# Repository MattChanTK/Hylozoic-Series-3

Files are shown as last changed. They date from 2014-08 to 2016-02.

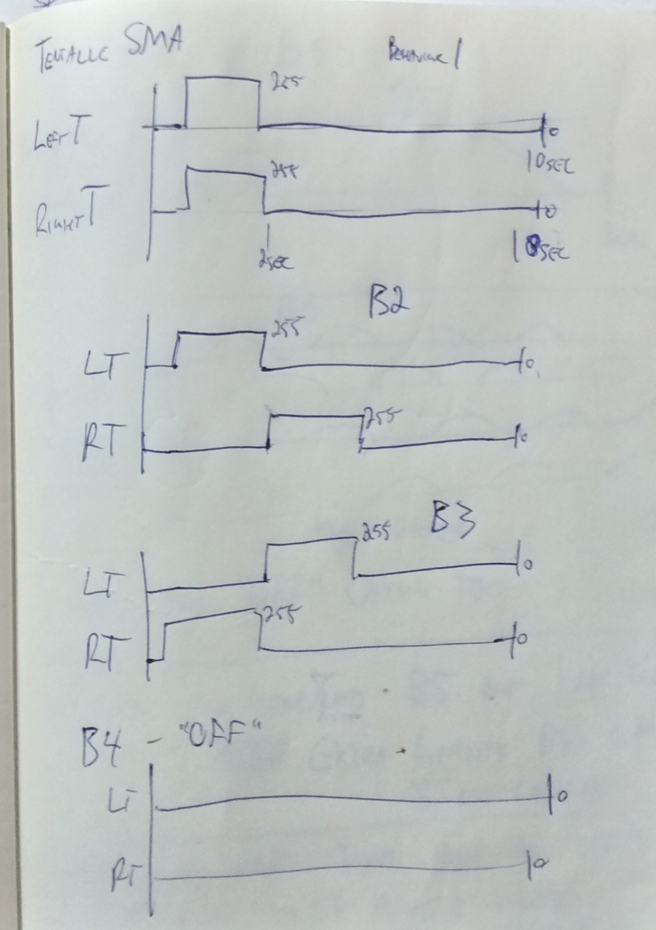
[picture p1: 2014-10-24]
Software/teensy_firmware/HK_Unit_Teensy/Wave_form_sketch.jpg

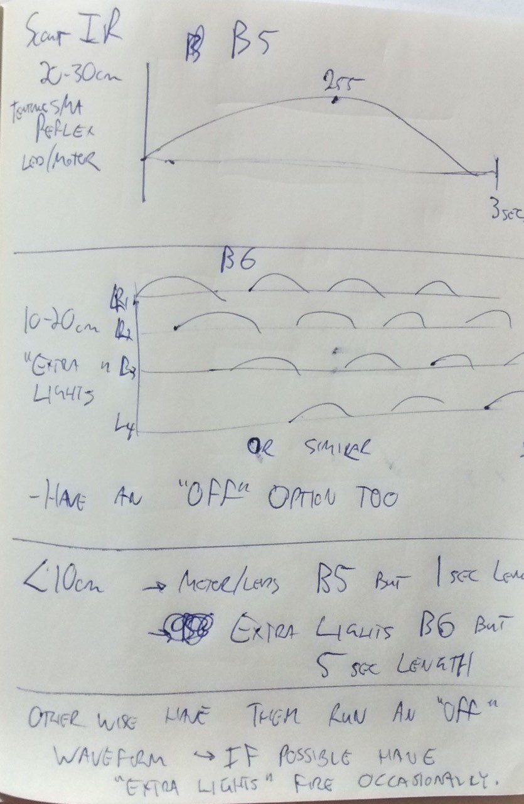
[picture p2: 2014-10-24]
Software/teensy_firmware/HK_Unit_Teensy/Wave_form_sketch_2.jpg

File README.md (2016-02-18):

Hylozoic Series 3 Interactive Control System
======================

 Combining techniques in architecture, the arts, electronics, and software, the Living Architecture System Group (LASG) develops interactive art sculptures that engage occupants in an immersive environment. The overarching goal of this research is to develop architectural systems that possess life-like qualities. In the Hylozoic Series kinetic sculptures built by [Philip Beesley Architect Inc.](http://philipbeesleyarchitect.com/), the designers use a network of microcontrollers to control and sample a sizable number of actuators and sensors. Each node in the network can perform a simple set of interactive behaviours. Though complexity may emerge in previous systems through superposition of a set of simple and prescripted behaviours, the responses of the systems to occupants remain rather robotic and ultimately dictated by the will of the designers. 

To enable the sculpture to automatically generate interactive behaviours and
adapt to changes, [Curiosity-Based Learning Algorithm (CBLA)](https://ece.uwaterloo.ca/~dkulic/pubs/ChanIROS2015.pdf), a reinforcement learning algorithm which selects actions that lead to maximum potential knowledge gains, is introduced.

To realize the CBLA system on a physical interactive art sculpture, an overhaul of the previous series’ interactive control hardware was necessary. CBLA requires the system to be able to sense the consequences of its own actions and its surrounding at a much higher resolution and frequency than previously implemented behaviour algorithms. This translates to the need to interface and collect samples from a substantially larger number of sensors. 

The **Hylozoic Series 3 Interactive Control System** consists of a new set of hardware and control system software was developed. It enables the control and sampling of hundreds of devices on a centralized computer through USB connections. Moving the computation from an embedded platform simpliﬁes the implementation of the CBLA system, which is a computationally intensive and complex
program. In addition, the large amount of data generated by the system can now be recorded without sacriﬁcing response time nor resolution.

## Organizations

### Hardware

The electronics that interface with the sensors and actuators were mostly customly designed. The [schematic](Hardware/Design Files), [PCB design](Hardware/Design Files), BOM, as well as [fabrication files](Hardware/fabrication) (like Gerber and quotes) for previous production runs can be found in the [Hardware](Hardware) directory. 

### Software

The [firmware](Software/teensy_firmware) that runs on the Teensy microcontroller, the [Python-based software framework](Software/pyHylozoic3) (pyHylozoic3), and [installation-specific behaviours](Software/complex_behaviours) can be found in the [Software](Software) directory. In addition, some of the necessary [libraries](Software/_libraries), and some [basic demo codes](Software/basic_behaviours) can also be in the directory.

In addition to the [communication framework](Software/pyHylozoic3/interactive_system/interactive_system), the pyHylozoic3 module includes an implemenation of the [CBLA Engine](Software/pyHylozoic3/cbla/cbla/cbla_engine), and [Abstract Node system](Software/pyHylozoic3/abstract_node/abstract_node) that supports the deployments of a network of multiple [CBLA Nodes](Software/pyHylozoic3/cbla/cbla).

## Contributors
* Matthew Tsz Kiu Chan (University of Waterloo)
* Mohammedreza Memarian (University of Waterloo)
* Matt Borland (Philip Beesley Architect Inc.)
* David Kadish (Philip Beesley Architect Inc.)

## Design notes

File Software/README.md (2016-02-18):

# Hylozoic Series 3 Software

## pyHylozoic3

The pyHylozoic3 directory is a set of Python Modules that make up the Hylozoic Series 3 software framework and its key features. It is written for Python 3.4+ (with libraries packaged with [Anaconda](https://www.continuum.io/downloads)) and tested on Windows 7, 8, 8.1, and 10. To install, run the [*install_pyHylozoic3.bat*](pyHylozoic3/install_pyHylozoic3.bat). To communicate with Teensy devices over USB, [libusb0.1](http://www.libusb.org/) is also required. Its installation files for Windows PC can be found in the [libraries](_libraries) directory.

## Firmware (teensy_firmware)

For different hardware configurations, different firmware (written in Arduino/C++) is required. This firmware goes with a matching set of [pyHylozoic3](pyHylozoic3) based communication protocol and behaviours code. Common utilities and base class files can be found in the [libraries](libraries) directory.

In the [teensy_firmware](teensy_firmware) directory, there are also standalone software that does not require the use of [pyHylozoic3](pyHylozoic3).

## Complex Behaviours (complex_behaviours)

Complex projects that use the [abstract_node](pyHylozoic3/abstract_node/abstract_node) module in the [pyHylozoic3](pyHylozoic3) are located in the [complex_behaviours](complex_behaviours) directory. This includes system that runs [CBLA](pyHylozoic3/cbla/cbla) and more elaborate prescripted behaviours. In addition, [hmi_gui](pyHylozoic3/hmi_gui/hmi_gui) can also be used to create a simple GUI that outputs internal data and basic textbox-based controls.

## Basic Behaviours (basic_behaviours)

Simple test or demo codes that only uses the [interactive_system](pyHylozoic3/interactive_system) module are found in the [basic_behaviours](basic_behaviours) directory.
Example basic behaviours include [basic actuation cycling](basic_behaviours/Behaviours.py), [End-Of-Line testing script](basic_behaviours/EOL_Tool.py), and [internode test](basic_behaviours/Behaviours.py) that demonstrated the possibilibity of nehgbourhood behaviours.

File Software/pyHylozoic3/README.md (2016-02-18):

# pyHylozoic3

## Interactive System ([interactive_system](interactive_system/interactive_system))

It is a Python module that was written to enable the communication with many Teensy devices simultaneously. A Teensy-Interface thread is created for each Teensy device and synchronize the copies of the hash tables on the Teensy and the computer continuously. Applications on the computer side can control and sample the states of the Teensy devices by modifying the values in the hash tables.

## Abstract Node Layer ([abstract_node](abstract_node/abstract_node))

An additional layer of abstraction was built to represent the sculpture as a network of node. Each node runs as its own thread and possesses a set of input and output variables. Behaviour of each node can be programmed individually. A pre-scripted version of the behaviours will be programmed to compare with the CBLA version in user studies.

## Curiosity Driven Learning Algorithm ([cbla](cbla/cbla))
The CBLA is a type of reinforcement learning algorithm, where the reduction of prediction error is the reward. During the learning process, it will explore regions of the state space that are neither too predictable nor too random; it wants to focus on areas that have the highest potential for new knowledge. To structure the learning process and identify interesting
regions of the state-space, the CBLA automatically segments the state-space into regions; an expert in each region makes predictions about the effects of an action and adjusts its prediction model based on the actual resultant state. The value of each expert is determined by its record of error reduction. This value will then determine the execution likelihood of the action associated with this expert.

## GUI ([hmi_gui](hmi_gui/hmi_gui), [custom_gui](custom_gui/custom_gui))
A basic GUI that display values of input, output, and internal variables. It's based on [Tkinter](https://wiki.python.org/moin/TkInter). A textbox can also be added to change values of the the output variables. *custom_gui* implemented installation-specific GUI.

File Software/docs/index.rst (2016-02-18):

.. Hylozoic Series 3 documentation master file, created by
   sphinx-quickstart on Thu Jan 28 16:36:26 2016.
   You can adapt this file completely to your liking, but it should at least
   contain the root `toctree` directive.

Welcome to Hylozoic Series 3's documentation!
=============================================

**pyHylozoic3** is a set of Python modules that provide the key features introduced in the Hylozoic Series 3 system. 

- interactive_system_ provides the infrastructures that enable a client running a pyHylozoic3 program to communicate with a distributed set of microconstrollers.

- abstract_node_ enables the creation of a network of asychronous threads that describe the behaviour of the system.

- hmi_gui_ provides a basic GUI that is compatible the *abstract_node* system.

- custom_gui_ provides a set of customized GUI based on *hmi_gui* that tailors to a handful of operation modes.

- cbla_ contains the CBLA Engine and the implementation of a generic CBLA Node.

.. _interactive_system: ./_apidoc/interactive_system/modules.html
.. _abstract_node: ./_apidoc/abstract_node/modules.html
.. _hmi_gui: ./_apidoc/hmi_gui/modules.html
.. _custom_gui: ./_apidoc/custom_gui/modules.html
.. _cbla: ./_apidoc/cbla/modules.html

**complex_behaviours** contains a handful of specific implementations that use the *pyHylozoic3* Module.

- *pbai_fin_test_bed* contains the implementation of manual, prescipted, and CBLA type behaviours for the CBLA Fin Test Bed.

- *cbla_test_bed* contains the implementation of CBLA behaviours for the CBLA Test Bed used during development and validation of the CBLA. This behaviour does not use the *cbla* module in *pyHylozoic3*. Instead, its CBLA Engine and CBLA Nodes are embedded to protect the integrity of the system.

- *washington_demo* contains the work-in-progress for the Sound Test Bed that is primarily used for demostration purposes in Washington and perhaps CITA.

Contents:

.. toctree::
   :maxdepth: 2
   
   ./installing

Communications Protocol
=======================
There is no standard protocol because every configuration has a different set of hardware attached.
So for each installation, we would need to write a different set of protocols.
   
Terminology
===========
Nodes are hierarchial and can comprise of other nodes (i.e. nodes can be sets of nodes).
But at their most basic level each sensor or actuator can be its own node and nodes can consist of inputs and/or outputs.

Indices and tables
==================

* :ref:`genindex`
* :ref:`modindex`
* :ref:`search`

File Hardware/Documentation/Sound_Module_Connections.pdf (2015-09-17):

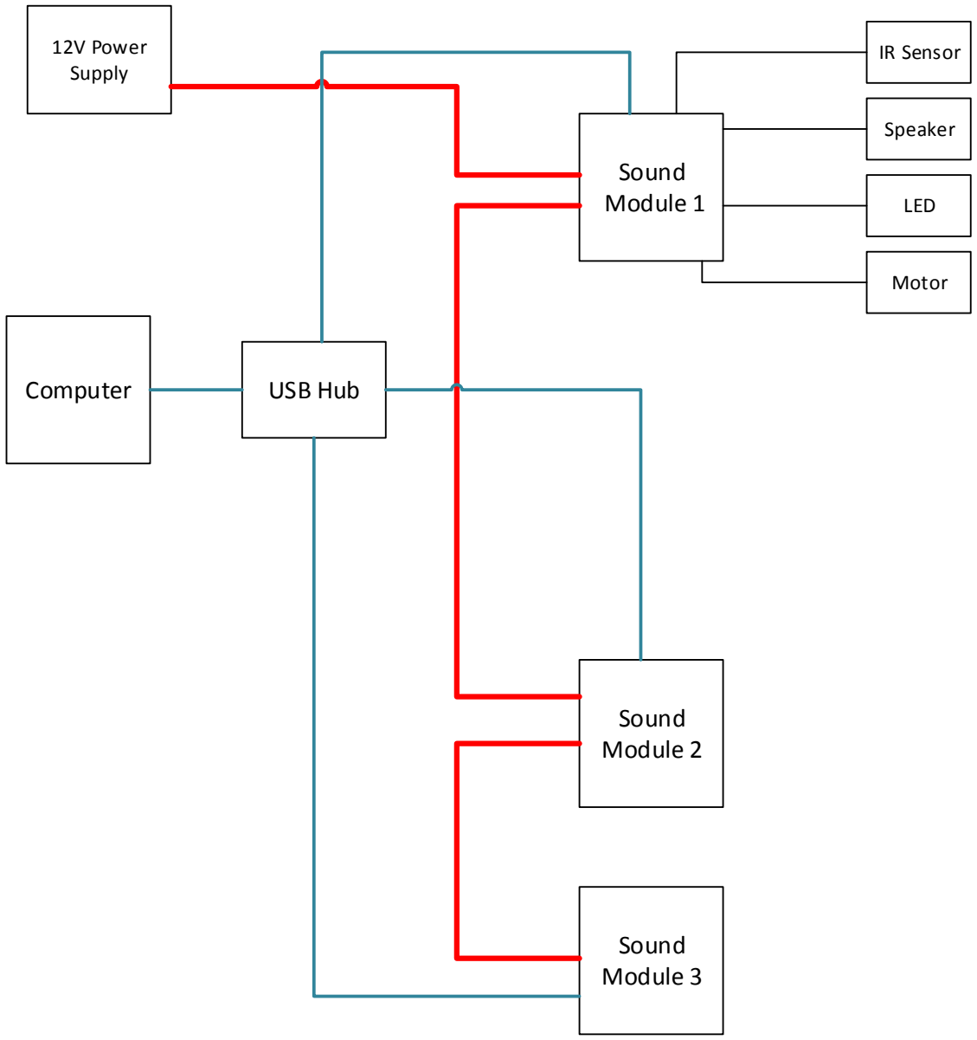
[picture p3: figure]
Sound Module 1; 12V Power Supply; Sound Module 2; Sound Module 3; Computer; USB Hub; IR Sensor; Speaker; LED; Motor

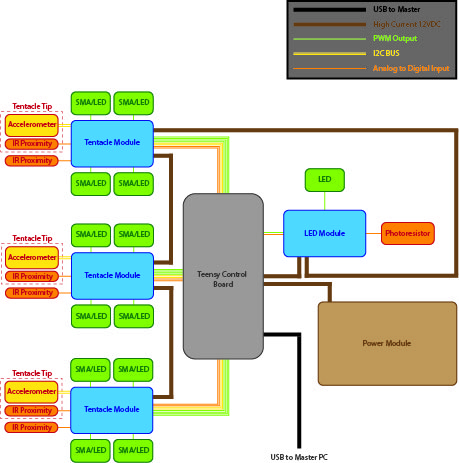
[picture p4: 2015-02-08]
Hardware/Documentation/High-level Electronic Block Diagram.jpg

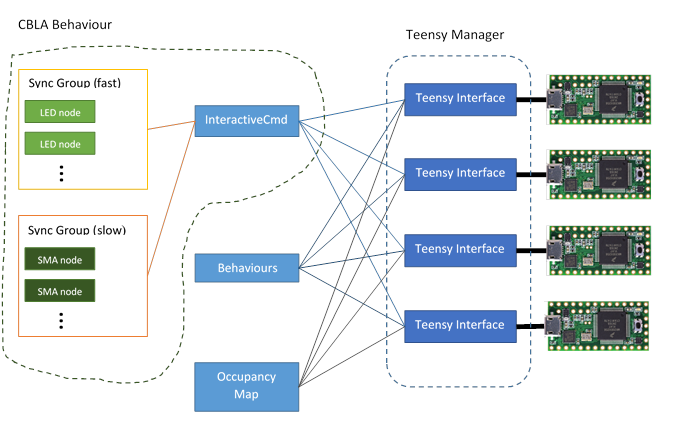
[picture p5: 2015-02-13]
Software/_documentation/diagrams/Software Overall Network Architecture.png

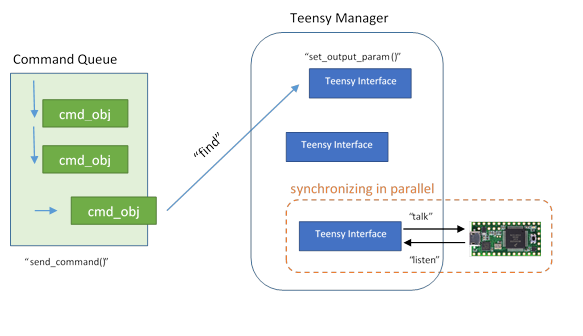
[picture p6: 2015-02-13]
Software/_documentation/diagrams/Software InteractiveCmd Block Diagram.png

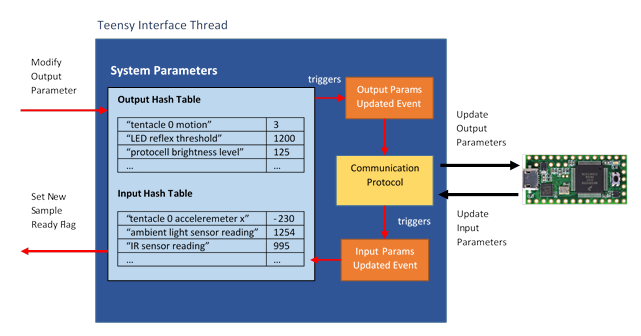
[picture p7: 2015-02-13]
Software/_documentation/diagrams/Software Teensy Interface Block Diagram.png

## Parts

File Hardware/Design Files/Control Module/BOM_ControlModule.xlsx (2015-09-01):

 | Control Module Bill of Materials (BOM)
Item # | Ref Des | Description | Qty | Manufacturer | Mfg Part # | Package | Type | Your Instructions | Total Required for 10 Boards | Packed
1 | JP2, JP3 | CONN HEADER .100" SNGL STR 3POS | 2 | Sullins Connector Solutions | PREC003SAAN-RC | 0.100" (2.54mm) | thru-hole |  | 20 | 24
2 | LED1, LED2, LED3 | LED 3.2X1.6MM 568NM GRN CLR SMD | 3 | Kingbright | APTR3216SGC | 1206 | SMD |  | 30 | 34
3 | SV3, SV4, SV5, SV6, SV7, SV8 | CONN HEADER FEMALE 8 POS .1" TIN | 6 | Sullins Connector Solutions | PPTC081LFBN-RC | 0.100" (2.54mm) | thru-hole |  | 0 | 0
4 | X1 | CONN HEADER FEMALE 2 POS .1" TIN | 1 | Sullins Connector Solutions | PPTC021LFBN-RC | 0.100" (2.54mm) | thru-hole |  | 0 | 0
5 | X7, X9 | TERMINAL BLOCK 5.08MM 2POS PCB | 4 | On Shore Technology Inc | OSTTG025100B | 0.200" pitch | thru-hole |  | 40 | 0
6 | C4, C5 | CAP CER 0.1UF 50V Y5V 0603 | 2 | Samsung Electro-Mechanics America, Inc | CL10F104ZB8NNNC | 0603 | SMD |  | 20 | 20
7 | C2, C3 | CAP CER 1UF 25V 10% X5R 0603 | 2 | Murata Electronics North America | GRM188R61E105KA12D | 0603 | SMD |  | 20 | 20
8 | R7, R8 | RES 2.2K OHM 1/10W 5% 0603 | 2 | Samsung Electro-Mechanics America, Inc | RC1608J222CS | 0603 | SMD |  | 20 | 20
9 | R1, R4, R5 | RES 470 OHM 1/4W 5% 0603 SMD | 3 | Rohm Semiconductor | RHM470DCT-ND | 0603 | SMD |  | 30 | 30
10 | C1 | CAP ALUM 470UF 25V 20% RADIAL | 1 | Panasonic Electronic Components | EEU-FR1E471Y | 0.315" Dia | thru-hole |  | 10 | 13
11 | R2, R3, R6 | RES 4.7K OHM 1/10W 5% 0603 SMD | 3 | Yageo | RC0603JR-074K7L | 0603 | SMD |  | 30 | 30
12 | U2, U3 | IC MUX/DEMUX 8X1 16TSSOP | 2 | NXP Semiconductors | 74HC4051PW,118 | 16-TSSOP | SMD |  | 20 | 20
13 | IC1 | IC REG LDO 5V 1A DPAK | 1 | ON Semiconductor | MC7805BDTRKG | TO-252-3 | SMD |  | 10 | 10
14 | U1 | IC PWM CTLR LED DVR 28TSSOP | 1 | NXP Semiconductors | PCA9685PW/Q900,118 | 28-TSSOP | SMD |  | 10 | 10
15 | Q1 | MOSFET N-CH 60V 300MA SOT-23 | 1 | Vishay Siliconix | 2N7002K-T1-E3TR-ND | SOT-23-3 |  |  | 10 | 14
16 | SV1 | CONN HEADER FEMALE 4POS .1" TIN | 1 | Sullins Connector Solutions | PPTC041LFBN-RC | 0.100" (2.54mm) | thru-hole |  | 10 | 0
17 | D1 | DIODE SCHOTTKY 40V 5A DO201AD | 1 | Comchip Technology | SB540E-G | DO-201AD, Axial | thru-hole |  | 10 | 12
18 | SV2 | CONN HEADER FMALE 8PS .1" DL TIN | 1 | Sullins Connector Solutions | PPTC042LFBN-RC | 0.100" (2.54mm) | thru-hole |  | 10 | 0
19 | U$2 | CONN HEADER FEMALE 3 POS .1" TIN | 1 | Sullins Connector Solutions | PPPC031LFBN-RC | 0.100" (2.54mm) | thru-hole |  | 10 | 10
 |  | CONN HEADER FEMALE 5 POS .1" TIN | 3 | Sullins Connector Solutions | PPTC051LFBN-RC | 0.100" (2.54mm) | thru-hole |  | 30 | 0
 |  | CONN HEADER FEMALE 13 POS .1" TIN | 2 | Sullins Connector Solutions | PPTC131LFBN-RC | 0.100" (2.54mm) | thru-hole |  | 20 | 0
20 | IC2 | IC REG LDO 3.3V 0.5A TO252-3 | 1 | Texas Instruments | UA78M33CKVURG3 | TO-252-3 | SMD |  | 10 | 12
21 | X8 | CONN HEADER FEMALE 2 POS .1" TIN | 1 | Sullins Connector Solutions | PPTC021LFBN-RC | 0.100" (2.54mm) | thru-hole |  | 0 | 0

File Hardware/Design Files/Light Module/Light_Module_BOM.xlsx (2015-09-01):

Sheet: Light Module
 | Light Module Bill of Materials (BOM)
Item # | Ref Des | Description | Qty | Manufacturer | Mfg Part # | Package | Type | Your Instructions
1 | X8 | CONN MOD JACK 4P4C VERT UNSHLD | 1 | Assmann WSW Components | A-2014-3-4-N-T-R |  | thru-hole
2 | JP1 | CONN HEADER .100" SNGL STR 3POS | 1 | Sullins Connector Solutions | PREC003SAAN-RC | 0.100" (2.54mm) | thru-hole
3 | LED1 | LED 3.2X1.6MM 568NM GRN CLR SMD | 1 | Kingbright | APTR3216SGC | 1206 | SMD
4 | T1 | MOSFET N-CH 60V 18A 43MOHM DPAK | 1 | ON Semiconductor | NTD5867NLT4G | TO-252-3 | SMD
5 | X4 | CONN HEADER MALE 2 POS .1" TIN | 1 | Sullins Connector Solutions | PREC002SAAN-RC | 0.100" (2.54mm) | thru-hole
6 | X7 | CONN HEADER MALE 3 POS .1" TIN | 1 | Sullins Connector Solutions | PREC003SAAN-RC | 0.100" (2.54mm) | thru-hole
7 | X1 | TERMINAL BLOCK 5.08MM 2POS PCB | 2 | On Shore Technology Inc | OSTTG025100B | 0.200" pitch | thru-hole
8 | X6 | TERMINAL BLOCK 5.08MM 2POS PCB | 1 | On Shore Technology Inc | OSTTG025100B | 0.200" pitch | thru-hole
9 | C2, C3 | CAP CER 1UF 25V 10% X5R 0603 | 2 | Murata Electronics North America | GRM188R61E105KA12D | 0603 | SMD
10 | R2 | RES 4.7K OHM 1/10W 5% 0603 SMD | 1 | Yageo | RC0603JR-074K7L | 0603 | SMD
11 | R1 | RES 470 OHM 1/4W 5% 0603 SMD | 1 | Rohm Semiconductor | RHM470DCT-ND | 0603 | SMD
12 | C1 | CAP ALUM 470UF 25V 20% RADIAL | 1 | Panasonic Electronic Components | EEU-FR1E471Y | 0.315" Dia | thru-hole
13 | R3 | RES 5.6 OHM 5W 5% AXIAL | 1 | Yageo | SQP500JB-5R6 |  | thru-hole
14 | IC1 | IC REG LDO 5V 1A DPAK | 1 | ON Semiconductor | MC7805BDTG | TO-252-3 | SMD
15 | X3 | CONN MOD JACK R/A 8P8C | 1 | FCI | 54602-908LF |  | thru-hole
16 | D1 | DIODE SCHOTTKY 40V 5A DO201AD | 1 | Comchip Technology | SB540E-G | DO-201AD, Axial | thru-hole

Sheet: Sheet1
 | Light Module Bill of Materials (BOM)
Item | Ref Des | Description | Value | Qty | Device | Package
1 | X8 | AMP connector |  | 1 | 558872-1
1 | JP1 | JUMPER |  | 1 | JP2E
1 | LED1 | LED |  | 1 | LEDSML1206
1 | T1 | MOS FET |  | 1 | NTD5867NLT4G
1 | X4 | PIN HEADER |  | 1 | PINHD-1X2
1 | X7 | PIN HEADER |  | 1 | PINHD-1X3
1 | X1 | WAGO SREW CLAMP |  | 1 | W237-04P
1 | X6 | WAGO SCREW CLAMP |  | 1 | W237-102
2 | C2, C3 | CAPACITOR, American symbol | 1uF | 2 | C-USC0603
1 | R2 | RESISTOR, American symbol | 4.7k | 1 | R-US_R0603
1 | R1 | RESISTOR, American symbol | 470 | 1 | R-US_R0603
1 | C1 | POLARIZED CAPACITOR, American symbol | 470uF | 1 | CPOL-USE5-10.5
1 | R3 |  | 5.6 | 1 | SQP500JB-5R6
1 | IC1 | 1A Positive Voltage Regulators | MC7805BDTRKG | 1 | MC7805BDTRKG
1 | X3 | CORCOM Modular RJ Jacks No Shield | RJ45-8X | 1 | RJ45-8X
1 | D1 | SCHOTTKY BARRIER RECTIFIER 3.0 AMPERES 20, 30, 40 VOLT | SB540E-G | 1 | SB540E-G

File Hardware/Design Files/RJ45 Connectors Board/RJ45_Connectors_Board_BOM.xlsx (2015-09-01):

 | RJ45 Connector Board Bill of Materials (BOM)
Item # | Ref Des | Description | Qty | Manufacturer | Mfg Part # | Package | Type | Your Instructions | Total Required for 10 Boards | Packed
1 | LED1, LED2, LED3, LED4, LED5, LED6, LED7, LED8, LED9, LED10, LED11, LED12, LED13, LED14, LED15, LED16, LED17, LED18, LED19, LED20, LED21, LED22, LED23, LED24 | LED 3.2X1.6MM 568NM GRN CLR SMD | 24 | Kingbright | APTR3216SGC | 1206 | SMD |  | 240 | 0
2 | SV1, SV2, SV9, SV10, SV11, SV12 | CONN HEADER .100" SNGL STR 8POS | 6 | Sullins Connector Solutions | PREC008SAAN-RC | 0.100" (2.54mm) | thru-hole |  | 60 | 0
3 | X1 | CONN HEADER .100" SNGL STR 2POS | 1 | Sullins Connector Solutions | PREC002SAAN-RC | 0.100" (2.54mm) | thru-hole |  | 10 | 0
4 | X2 | CONN HEADER .100" SNGL STR 3POS | 1 | Sullins Connector Solutions | PREC003SAAN-RC | 0.100" (2.54mm) | thru-hole |  | 10 | 0
5 | IC1, IC2, IC3 | TRANS 8NPN DARL 50V 0.5A 18SOL | 3 | Toshiba Semiconductor and Storage | ULN2803AFWG,C,EL | 18-SOIC | SMD |  | 30 | 0
6 | R1, R2, R3, R4, R5, R6, R7, R8, R9, R10, R11, R12, R13, R14, R15, R16, R17, R18, R19, R20, R21, R22, R23, R24 | RES 470 OHM 1/4W 5% 0603 SMD | 24 | Rohm Semiconductor | RHM470DCT-ND | 0603 | SMD |  | 240 | 0
7 | SV3, SV4, SV5, SV6, SV7, SV8 | CONN MOD JACK 8P8C VERT UNSHLD | 6 | FCI | 69255-001LF |  | thru-hole |  | 60 | 63

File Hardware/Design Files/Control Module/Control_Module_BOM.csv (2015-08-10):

Partlist
Exported from Control_Module.brd at 2015-08-10 3:16 PM
EAGLE Version 7.3.0 Copyright (c) 1988-2015 CadSoft
Assembly variant:
Part     Value                        Package            Library                    Position (inch)       Orientation
C1       470uF                        E5-10,5            rcl                        (0.99 0.24)           MR90
C2       1uF                          C0603              rcl                        (0.3 0.64)            R90
C3       1uF                          C0603              rcl                        (0.3 0.14)            R270
C4       100nF                        C0603              rcl                        (0.3 0.49)            R270
C5       100nF                        C0603              rcl                        (0.3 0.29)            R90
D1       SB540E-G                     DO201T15           CBLA_Test_bed_Library      (2.48 0.61)           R0
IC1      MC7805BDTRKG                 DPACK_3            CBLA_Test_bed_Library      (0.63 0.54)           R90
IC2      UA78M33CKVU                  DPACK              CBLA_Test_bed_Library      (0.63 0.19)           R90
JP2                                   JP2                jumper                     (0.98 0.64)           R90
JP3                                   JP2                jumper                     (1.93 0.59)           R0
LED1                                  SML1206            led                        (2.77 0.43)           MR180
LED2                                  SML1206            led                        (0.46 0.54)           MR0
LED3                                  SML1206            led                        (0.46 0.25)           MR0
Q1       PROGRAM_FET                  SOT-23             transistors                (0.96 2.04)           R180
R1       470                          R0603              CBLA_Test_bed_Library      (2.59 0.43)           MR180
R2       4k7                          R0603              CBLA_Test_bed_Library      (1.16 0.61)           R270
R3       4k7                          R0603              CBLA_Test_bed_Library      (1.71 0.72)           R0
R4       470                          R0603              CBLA_Test_bed_Library      (0.47 0.13)           MR180
R5       470                          R0603              CBLA_Test_bed_Library      (0.46 0.44)           MR180
R6       4k7                          R0603              CBLA_Test_bed_Library      (0.97 2.21)           R0
R7       2.2k                         R0603              CBLA_Test_bed_Library      (1.08 1.32)           R270
R8       2.2k                         R0603              CBLA_Test_bed_Library      (1.85 1.69)           R270
SV1      PWM_I2C                      MA04-1             con-lstb                   (1.43 0.64)           R0
SV2      SPI                          MA04-2             con-lstb                   (0.71 2.99)           R0
SV3                                   MA08-1             con-lstb                   (0.18 2.69)           R270
SV4                                   MA08-1             con-lstb                   (0.18 1.89)           R270
SV5                                   MA08-1             con-lstb                   (0.18 1.09)           R270
SV6                                   MA08-1             con-lstb                   (2.78 2.69)           R90
SV7                                   MA08-1             con-lstb                   (2.78 1.89)           R90
SV8                                   MA08-1             con-lstb                   (2.78 1.09)           R90
U$2      TEENSY_3.1_ALL_PINS_AND_PADS TEENSY_3.1_ALLPINS Teensy_3_Series_Board_v1.0 (1.43 2.34)           R0
U1       PCA9685PW                    SOP65P640X110-28N  NXP_By_element14_Batch_1   (1.43 0.94)           R0
U2       74HC4051PW,118               SOP65P640X110-16N  NXP_By_element14_Batch_1   (1.43 1.29)           R0
U3       74HC4051PW,118               SOP65P640X110-16N  NXP_By_element14_Batch_1   (1.43 1.54)           R0
X1                                    1X02               CBLA_Test_bed_Library      (1.85 3.04)           R90
X7                                    W237-4P            con-wago-508               (2.47 0.2)            R0
X8       UART                         1X02               CBLA_Test_bed_Library      (1 2.99)              R90
X9                                    W237-4P            con-wago-508               (1.61 0.2)            R0

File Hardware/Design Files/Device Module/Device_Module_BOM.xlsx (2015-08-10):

 | Device Module Bill of Materials (BOM)
Item # | Ref Des | Description | Qty | Manufacturer | Mfg Part # | Package | Type | Your Instructions | Total Required for 22 Boards | Packed
1 | JP1, JP2, JP3 | CONN HEADER .100" SNGL STR 3POS | 3 | Sullins Connector Solutions | PREC003SAAN-RC | 0.100" (2.54mm) | thru-hole |  | 66 | 0
2 | LED1, LED2, LED3, LED4, LED5, LED6 | LED 3.2X1.6MM 568NM GRN CLR SMD | 6 | Kingbright | APTR3216SGC | 1206 | SMD |  | 132 | 140
3 | X11, X12, X13, X14 | PIN HEADER | 1 |  |  | 0.100" (2.54mm) | thru-hole | Leave unpopulated | 0 | 0
4 | X2 | CONN HEADER .100" SNGL STR 3POS | 1 |  |  | 0.100" (2.54mm) | thru-hole | Leave unpopulated | 0 | 0
5 | X15 | CONN HEADER .100" SNGL STR 3POS | 1 | PREC003SAAN-RC | PREC020SAAN-RC | 0.100" (2.54mm) | thru-hole |  | 22 | 0
6 | X4, X6 | CONN HEADER FEMALE 8POS .1" TIN | 2 | Sullins Connector Solutions | PPTC081LFBN-RC | 0.100" (2.54mm) | thru-hole |  | 44 | 0
7 | X1 | TERMINAL BLOCK 5.08MM 2POS PCB | 2 | On Shore Technology Inc | OSTTG025100B | 0.200" pitch | thru-hole | Put two 2p together to form a 4p | 44 | 120
8 | X7, X8, X9, X10 | TERMINAL BLOCK 5.08MM 2POS PCB | 4 | On Shore Technology Inc | OSTTG025100B | 0.200" pitch | thru-hole |  | 88
9 | C4, C5 | CAP CER 0.1UF 50V Y5V 0603 | 2 | Samsung Electro-Mechanics America, Inc | CL10F104ZB8NNNC | 0603 | SMD |  | 44 | 50
10 | C2, C3, C6, C7, C8, C9 | CAP CER 10UF 25V 10% X5R 1206 | 6 | Samsung Electro-Mechanics America, Inc | CL31A106KAHNNNE | 1206 | SMD |  | 132 | 140
11 | R4, R5, R6, R7 | RES 1.00K OHM .25W 1% 0603 SMD | 4 | Vishay Dale | CRCW06031K00FKEAHP | 0603 | SMD |  | 88 | 92
12 | R1 | RES 267 OHM 1/10W .1% 0603 SMD | 1 | Panasonic Electronic Components | ERA-3AEB2670V | 0603 | SMD |  | 22 | 25
13 | R8, R9, R10, R11 | RES 4.7K OHM 1/10W 5% 0603 SMD | 4 | Yageo | RC0603JR-074K7L | 0603 | SMD |  | 88 | 93
14 | R2, R3, R12, R13, R14, R15 | RES 470 OHM 1/4W 5% 0603 SMD | 6 | Rohm Semiconductor | RHM470DCT-ND | 0603 | SMD |  | 132 | 136
15 | C1 | CAP ALUM 470UF 25V 20% RADIAL | 1 | Panasonic Electronic Components | EEU-FR1E471Y | 0.315" Dia | thru-hole |  | 22 | 24
16 | IC2 | IC REG LDO 5V 1A DPAK | 1 | ON Semiconductor | MC7805BDTG | TO-252-3 | SMD |  | 22 | 24
17 | T1, T2, T3, T4 | MOSFET N-CH 60V 18A 43MOHM DPAK | 4 | ON Semiconductor | NTD5867NLT4G | TO-252-3 | SMD |  | 88 | 100
18 | IC1 | CONV DC/DC 6A 12VIN POL SIP | 1 | Murata Power Solutions Inc | OKR-T/6-W12-C | 5-SIP Module | thru-hole |  | 22 | 24
19 | X3, X5 | CONN MOD JACK R/A 8P8C | 2 | FCI | 54602-908LF |  | thru-hole |  | 44 | 50
20 | D1 | DIODE SCHOTTKY 40V 5A DO201AD | 1 | Comchip Technology | SB540E-G | DO-201AD, Axial | thru-hole |  | 22 | 24
21 | IC3 | IC REG LDO 3.3V 0.5A TO252-3 | 1 | Texas Instruments | UA78M33CKVURG3 | TO-252-3 | SMD |  | 22 | 25

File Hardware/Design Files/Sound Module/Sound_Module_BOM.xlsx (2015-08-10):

 | Sound Module Bill of Materials (BOM)_Bittele Electronics Inc.
Item # | Ref Des | Description | Qty | Manufacturer | Mfg Part # | Package | Type | Your Instructions | Total Required for 14 Boards | Packed
1 | LED1, LED2, LED3, LED4, LED5, LED6, LED7 | LED 3.2X1.6MM 568NM GRN CLR SMD | 7 | Kingbright | APTR3216SGC | 1206 | SMD |  | 98 | 100
2 | PINOUT | CONN HEADER .100" SNGL STR 8POS | 1 | Sullins Connector Solutions | PREC008SAAN-RC | 0.100" (2.54mm) | thru-hole |  | 14 | 0
3 | IC1, IC2, IC3, IC4 | IC REG LDO 5V 1A DPAK | 4 | IC REG LDO 5V 1A DPAK | MC7805BDTRKG |  |  |  | 56 | 60
4 | MOS1, MOS2 | MOSFET N-CH 60V 18A 43MOHM DPAK | 2 | ON Semiconductor | NTD5867NLT4G | TO-252-3 | SMD |  | 28 | 31
5 | AMP_1_2, AMP_2_2 | CONN HEADER .100" SNGL STR 2POS | 2 | Sullins Connector Solutions | PREC002SAAN-RC | 0.100" (2.54mm) | thru-hole |  | 28 | 0
6 | A_1, A_2, A_3, POWER_LED, X2, X3 | CONN HEADER .100" SNGL STR 3POS | 6 | Sullins Connector Solutions | PREC003SAAN-RC | 0.100" (2.54mm) | thru-hole |  | 84 | 0
7 | SD_1, SD_2 | CONN HEADER .100" SNGL STR 5POS | 2 | Sullins Connector Solutions | PREC005SAAN-RC | 0.100" (2.54mm) | thru-hole |  | 28 | 0
8 | AMP_1_1, AMP_2_1 | CONN HEADER .100" SNGL STR 7POS | 2 | Sullins Connector Solutions | PREC007SAAN-RC | 0.100" (2.54mm) | thru-hole |  | 28 | 0
9 | TAB_CONN | CONN HEADER .100" SNGL STR 5POS | 2 | Sullins Connector Solutions | PREC005SAAN-RC | 0.100" (2.54mm) | thru-hole | Put two single-row to make one double-row | 28 | 0
10 | POWER | TERMINAL BLOCK 5.08MM 2POS PCB | 2 | On Shore Technology Inc | OSTTG025100B | 0.200" pitch | thru-hole | Put two 2p together to form a 4p | 28 | 30
11 | R4, R6, R15 | RES SMD 10 OHM 1% 1/10W 0603 | 3 | Bourns Inc. | CR0603-FX-10R0GLFCT-ND | 0603 | SMD |  | 42 | 45
12 | C4, C5, C7, C12 | CAP CER 0.1UF 50V Y5V 0603 | 4 | Samsung Electro-Mechanics America, Inc | CL10F104ZB8NNNC | 0603 | SMD |  | 56 | 60
13 | R11, R13 | RES 1.00K OHM .25W 1% 0603 SMD | 2 | Vishay Dale | CRCW06031K00FKEAHP | 0603 | SMD |  | 28 | 32
14 | PWM1, PWM2, SPK-1, SPK-2 | TERMINAL BLOCK 3.5MM 2POS PCB | 4 | OSTTG025100B | OSTTG025100B | 3.5 mm pitch | thru-hole |  | 56 | 0
15 | C2, C3, C6, C11 | CAP CER 1UF 25V 10% X5R 0603 | 4 | Murata Electronics North America | GRM188R61E105KA12D | 0603 | SMD |  | 56 | 60
16 | R7, R8 | RES 2.2K OHM 1/10W 5% 0603 | 2 | Samsung Electro-Mechanics America, Inc | RC1608J222CS | 0603 | SMD |  | 28 | 32
17 | C1 | CAP ALUM 1000UF 25V 20% RADIAL | 1 | Panasonic Electronic Components | ECA-1EM102 | 0.394" Dia | thru-hole |  | 14 | 16
18 | R10, R12 | RES 4.7K OHM 1/10W 5% 0603 SMD | 2 | Yageo | RC0603JR-074K7L | 0603 | SMD |  | 28 | 32
19 | R1, R2, R3, R5, R14, R17, R18 | RES 470 OHM 1/4W 5% 0603 SMD | 7 | Rohm Semiconductor | RHM470DCT-ND | 0603 | SMD |  | 98 | 104
20 | C8, C9, C13 | CAP ALUM 470UF 25V 20% RADIAL | 3 | Panasonic Electronic Components | EEU-FR1E471Y | 0.315" Dia | thru-hole |  | 42 | 45
21 | TEENSY | CONN HEADER FEMALE 3 POS .1" TIN | 1 | Sullins Connector Solutions | PPPC031LFBN-RC | 0.100" (2.54mm) | thru-hole |  | 14 | 0
 |  | CONN HEADER FEMALE 5 POS .1" TIN | 3 | Sullins Connector Solutions | PPTC051LFBN-RC | 0.100" (2.54mm) | thru-hole |  | 42 | 0
 |  | CONN HEADER FEMALE 13 POS .1" TIN | 2 | Sullins Connector Solutions | PPTC131LFBN-RC | 0.100" (2.54mm) | thru-hole |  | 28 | 0
22 | JACK | CONN MOD JACK R/A 8P8C | 1 | FCI | 54602-908LF |  | thru-hole |  | 14 | 16
23 | D1 | DIODE SCHOTTKY 40V 5A DO201AD | 1 | Comchip Technology | SB540E-G | DO-201AD, Axial | thru-hole |  | 14 | 16

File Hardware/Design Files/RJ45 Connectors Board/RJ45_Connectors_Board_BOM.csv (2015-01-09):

Qty | Value | Device | Package | Parts | Description | MF | MPN | OC_FARNELL | OC_NEWARK
24 |  | LEDSML1206 | SML1206 | LED1, LED2, LED3, LED4, LED5, LED6, LED7, LED8, LED9, LED10, LED11, LED12, LED13, LED14, LED15, LED16, LED17, LED18, LED19, LED20, LED21, LED22, LED23, LED24 | LED
6 |  | MA08-1 | MA08-1 | SV1, SV2, SV9, SV10, SV11, SV12 | PIN HEADER |  |  | unknown | unknown
1 |  | PINHD-1X2 | 1X02 | X1 | PIN HEADER
1 |  | PINHD-1X3 | 1X03 | X2 | PIN HEADER
3 |  | ULN2803AFWG | SOP18 | IC1, IC2, IC3 | DRIVER ARRAY
24 | 470 | R-US_R0603 | R0603 | R1, R2, R3, R4, R5, R6, R7, R8, R9, R10, R11, R12, R13, R14, R15, R16, R17, R18, R19, R20, R21, R22, R23, R24 | RESISTOR, American symbol
6 | RJ45-8X | RJ45-8X | RJ45-NO-SHIELD | SV3, SV4, SV5, SV6, SV7, SV8 | CORCOM Modular RJ Jacks No Shield |  | RJ45-8X | unknown | 16R6101

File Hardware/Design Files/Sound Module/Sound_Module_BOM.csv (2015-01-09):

Qty | Value | Device | Package | Parts | Description | MF | MPN | OC_FARNELL | OC_NEWARK
7 |  | LEDSML1206 | SML1206 | LED1, LED2, LED3, LED4, LED5, LED6, LED7 | LED
1 |  | MA08-1 | MA08-1 | PINOUT | PIN HEADER |  |  | unknown | unknown
4 |  | MC7805BDTRKG | DPACK_3 | IC1, IC2, IC3, IC4 | 1A Positive Voltage Regulators
2 |  | NTD5867NLT4G | DPACK | MOS1, MOS2 | MOS FET
2 |  | PINHD-1X2 | 1X02 | AMP_1_2, AMP_2_2 | PIN HEADER
6 |  | PINHD-1X3 | 1X03 | A_1, A_2, A_3, POWER_LED, X2, X3 | PIN HEADER
2 |  | PINHD-1X5 | 1X05 | SD_1, SD_2 | PIN HEADER
2 |  | PINHD-1X7 | 1X07 | AMP_1_1, AMP_2_1 | PIN HEADER
1 |  | PINHD-2X5 | 2X05 | TAB_CONN | PIN HEADER
1 |  | W237-04P | W237-4P | POWER | WAGO SREW CLAMP |  |  | unknown | unknown
3 | 10 | R-US_R0603 | R0603 | R4, R6, R15 | RESISTOR, American symbol
4 | 100nF | C-USC0603 | C0603 | C4, C5, C7, C12 | CAPACITOR, American symbol
2 | 1K | R-US_R0603 | R0603 | R11, R13 | RESISTOR, American symbol
4 | 1X2-3.5MM | 1X2-3.5MM | 1X2-3.5MM | PWM1, PWM2, SPK-1, SPK-2 | 3.5mm Terminal block
4 | 1uF | C-USC0603 | C0603 | C2, C3, C6, C11 | CAPACITOR, American symbol
2 | 2.2k | R-US_R0603 | R0603 | R7, R8 | RESISTOR, American symbol
1 | 2000uF | CPOL-USE5-10.5 | E5-10,5 | C1 | POLARIZED CAPACITOR, American symbol
2 | 4.7K | R-US_R0603 | R0603 | R10, R12 | RESISTOR, American symbol
7 | 470 | R-US_R0603 | R0603 | R1, R2, R3, R5, R14, R17, R18 | RESISTOR, American symbol
3 | 470uF | CPOL-USE5-10.5 | E5-10,5 | C8, C9, C13 | POLARIZED CAPACITOR, American symbol
1 | AUDIO BOARD | TEENSY_3.1_ALL_PINS_AND_PADS | TEENSY_3.1_ALLPINS | TEENSY | Footprint for Teensy 3.1 board using all pads and all through-holes. Pads need a 2x7 0.1 SMD header."
1 | RJ45-6L-B | RJ45-6L-B | RJ45-NO-SHIELD | JACK | CORCOM Modular RJ Jacks No Shield |  | RJ45-6L-B | unknown | 16R6090
1 | SB540E-G | SB540E-G | DO201T15 | D1 | SCHOTTKY BARRIER RECTIFIER 3.0 AMPERES 20, 30, 40 VOLT

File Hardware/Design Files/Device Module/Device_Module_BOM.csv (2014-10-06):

Qty | Value | Device | Package | Parts | Description | MF | MPN | OC_FARNELL | OC_NEWARK
3 |  | JP2E | JP2 | JP1, JP2, JP3 | JUMPER
6 |  | LEDSML1206 | SML1206 | LED1, LED2, LED3, LED4, LED5, LED6 | LED
4 |  | PINHD-1X2/90 | 1X02/90 | X11, X12, X13, X14 | PIN HEADER
2 |  | PINHD-1X3/90 | 1X03/90 | X2, X15 | PIN HEADER
2 |  | PINHD-1X8 | 1X08 | X4, X6 | PIN HEADER
1 |  | W237-04P | W237-4P | X1 | WAGO SREW CLAMP |  |  | unknown | unknown
4 |  | W237-102 | W237-102 | X7, X8, X9, X10 | WAGO SCREW CLAMP |  | 237-102 | unknown | 70K9898
2 | 100nF | C-USC0603 | C0603 | C4, C5 | CAPACITOR, American symbol
6 | 10uF | C-USC1206 | C1206 | C2, C3, C6, C7, C8, C9 | CAPACITOR, American symbol
4 | 1K | R-US_R0603 | R0603 | R4, R5, R6, R7 | RESISTOR, American symbol
1 | 267 | R-US_R0603 | R0603 | R1 | RESISTOR, American symbol
4 | 4.7K | R-US_R0603 | R0603 | R8, R9, R10, R11 | RESISTOR, American symbol
6 | 470 | R-US_R0603 | R0603 | R2, R3, R12, R13, R14, R15 | RESISTOR, American symbol
1 | 470uF | CPOL-USE5-10.5 | E5-10,5 | C1 | POLARIZED CAPACITOR, American symbol
1 | MC7805BDTRKG | MC7805BDTRKG | DPACK_3 | IC2 | 1A Positive Voltage Regulators
4 | NTD5867NL | NTD5867NLT4G | DPACK | T1, T2, T3, T4 | MOS FET
1 | OKR-T/10-W12 | OKR-T/10-W12 | OKR-C90 | IC1 | 5V/10A Murata POL DC/DC Converter
2 | RJ45-8X | RJ45-8X | RJ45-NO-SHIELD | X3, X5 | CORCOM Modular RJ Jacks No Shield |  | RJ45-8X | unknown | 16R6101
1 | SB540E-G | SB540E-G | DO201T15 | D1 | SCHOTTKY BARRIER RECTIFIER 3.0 AMPERES 20, 30, 40 VOLT
1 | UA78M33CKVU | UA78M33CKVU | DPACK | IC3 | Linear Voltage Reg

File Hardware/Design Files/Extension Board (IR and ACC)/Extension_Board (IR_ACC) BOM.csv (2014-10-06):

Qty | Value | Device | Package | Parts | Description | MF | MPN | OC_FARNELL | OC_NEWARK
1 |  | PINHD-1X3/90 | 1X03/90 | X2 | PIN HEADER
2 | 0.1uF | C-USC0603 | C0603 | C2, C3 | CAPACITOR, American symbol
1 | 10uF | C-USC1206 | C1206 | C1 | CAPACITOR, American symbol
2 | 2.2k | R-US_R0603 | R0603 | R1, R2 | RESISTOR, American symbol
1 | ADXL345 | ADXL345LONG | LGA14_LONG | U1
1 | RJ45-8X | RJ45-8X | RJ45-NO-SHIELD | X3 | CORCOM Modular RJ Jacks No Shield |  | RJ45-8X | unknown | 16R6101

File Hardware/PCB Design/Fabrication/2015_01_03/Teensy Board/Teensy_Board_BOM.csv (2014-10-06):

Qty | Value | Device | Package | Parts | Description | MF | MPN | OC_FARNELL | OC_NEWARK | PACKAGE | SUPPLIER
2 |  | JP2E | JP2 | JP2, JP3 | JUMPER
3 |  | LEDSML1206 | SML1206 | LED1, LED2, LED3 | LED
6 |  | MA08-1 | MA08-1 | SV3, SV4, SV5, SV6, SV7, SV8 | PIN HEADER |  |  | unknown | unknown
2 |  | R-US_R0603 | R0603 | R7, R8 | RESISTOR, American symbol
3 |  | W237-04P | W237-4P | X7, X9, X10 | WAGO SREW CLAMP |  |  | unknown | unknown
2 | 100nF | C-USC0603 | C0603 | C4, C5 | CAPACITOR, American symbol
2 | 1uF | C-USC0603 | C0603 | C2, C3 | CAPACITOR, American symbol
3 | 470 | R-US_R0603 | R0603 | R1, R4, R5 | RESISTOR, American symbol
1 | 470uF | CPOL-USE5-10.5 | E5-10,5 | C1 | POLARIZED CAPACITOR, American symbol
3 | 4k7 | R-US_R0603 | R0603 | R2, R3, R6 | RESISTOR, American symbol
2 | 74HC4051PW,118 | 74HC4051PW,118 | SOP65P640X110-16N | U2, U3 | 8-channel analog multiplexer/demultiplexer |  | 74HC4051PW,118 | 1826843 | 78R6260 | TSSOP-16 | NXP
1 | MC7805BDTRKG | MC7805BDTRKG | DPACK_3 | IC1 | 1A Positive Voltage Regulators
1 | PCA9685PW | PCA9685PW | SOP65P640X110-28N | U1 | 16-channel, 12-bit PWM Fm+ I2C-bus LED controller |  | PCA9685PW | 1854074 | 19T6398 | TSSOP-28 | NXP
1 | PROGRAM_FET | 2N7002_SOT23 | SOT-23 | Q1 | 2N7000, 2N7002, NDS7002A
1 | PWM_I2C | MA04-1 | MA04-1 | SV1 | PIN HEADER |  |  | unknown | unknown
6 | RJ45-8X | RJ45-8X | RJ45-NO-SHIELD | X1, X2, X3, X4, X5, X6 | CORCOM Modular RJ Jacks No Shield |  | RJ45-8X | unknown | 16R6101
1 | SB540E-G | SB540E-G | DO201T15 | D1 | SCHOTTKY BARRIER RECTIFIER 3.0 AMPERES 20, 30, 40 VOLT
1 | SPI | MA04-2 | MA04-2 | SV2 | PIN HEADER |  |  | unknown | unknown
1 | TEENSY_3.1_ALL_PINS_AND_PADS | TEENSY_3.1_ALL_PINS_AND_PADS | TEENSY_3.1_ALLPINS | U$2 | Footprint for Teensy 3.1 board using all pads and all through-holes. Pads need a 2x7 0.1 SMD header."
1 | UA78M33CKVU | UA78M33CKVU | DPACK | IC2 | Linear Voltage Reg
1 | UART | PINHD-1X2 | 1X02 | X8 | PIN HEADER

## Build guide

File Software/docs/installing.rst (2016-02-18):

.. How to install Hylozoic Series 3 Software

Installing pyHylozoic3 Software
=====================================

Install Python 3.3+ (Anaconda)
-----------------------------
Anaconda can be downloaded here: https://www.continuum.io/downloads. 

**IMPORTANT**: Download the one for Python 3.x only. The one for Python 2.7 would not work!

Download the PBLA software from github
--------------------------------------
Git Respository: https://github.com/dkadish/Hylozoic-Series-3

Install the pyHylozoic3 Software
--------------------------------
Under the Software/pyHylozoic3/ directory, run install_pyHylozoic3.bat

Install the USB drivers
-----------------------
Under Software/_libraries/libusb-win32-bin-1.2.6.0/bin, run inf-wizard.exe on all of the Teensyduino Interface 0's that you find.

Follow the instructions in libusb-win32-bin-README.txt.

Go to the AMD64 subdirectory and run install-filter-win.exe and select Install A Device Filter.
Next. Find VID: 16c0 and PID:0486, ending in mi:00.
Install that one.

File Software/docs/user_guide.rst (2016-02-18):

pyHylozoic3 Software User Guide
=====================================

Installing the pyHylozoic3 Software
--------------------------------
Under the Software/pyHylozoic3/ directory, run install_pyHylozoic3.bat.

The *python* keyword must  be set to execute Python 3.4+. 
Additional steps might be required in install libusb0 which is necessary for a *pyHylozoic3* system to run.

Software Overview
---------------------------------

The control software of the sculpture consists of a low-level firmware layer and high-level application layer. The two layers are connected via USB. The low-level layer consists of the firmware that interfaces with the peripherals that connect with the actuators and sensors. It resides on a custom Control Module that interfaces with the physical electronic components. The high-level layer consists of the tools that facilitate communication between the two layers and the application that dictates the system behaviour. The abstraction provided by the high-level layer allows flexibility in defining the nodes and their relationships to each other. 

A low-level layer of firmware written in C++ runs on the Teensy 3 USB-based development boards which interface with the peripherals that connect with the actuators and sensors. High-level software written in Python 3.4 runs on a central computer. The use of the central computer as a development platform provides flexibility for development free from the limited processing power and specialized functions inherent to the Teensy microcontroller hardware. 

Moreover, Python 3.4 is cross-platform and supports multi-threading, permitting operation within many operating systems and allowing multiple sets of software instructions to be executed in parallel. Code that is necessary for communicating with the low-level layer is packed into a Python module named *interactive-system*. Developers can then develop applications that control and retrieve information from the sculptural system firmware using the software utilities provided by the Python Package. Each application can run on its own thread. While care should be exercised to avoid conflicts among threads, this should permit multiple applications to execute simultaneously.	

A pyHylozoic3 system executes as an application that communicates with the low-level layer by extending the *interactive-system* Python module. Other applications such as an occupancy map that uses the sensors on the sculpture to interpret the locations of the occupants can run simultaneously, taking advantage of the multi-threading properties of the high-level platform.

At the high-level layer, the Teensy Interface module in the *interactive-system* package is used to create a thread for each Teensy device. The thread looks for changes in those parameters and performs synchronization. Each Teensy device on the low-level layer is represented by a Teensy Interface thread on the high-level layer. Teensy devices are considered as slave devices in this communication mechanism. Only the Teensy Interface, the Master, can initiate a read or write request. An InteractiveCmd thread can modify a Teensy's output parameters and retrieve its input parameters through its Teensy Interface. A communication protocol must be defined for each implementation and it is paired with a corresponding Teensy firmware. 

Between the Nodes and the Teensy Interface, there is the InteractiveCmd. Its job is to forward messages to the correct Teensy Interface and hide the physical implementation of the low-level layer devices from the Nodes. In addition, since the InteractiveCmd module enables the control and sampling of any actuators and sensors in the system, a Node can be constructed unconstrained by spatial or hardware specificities. Each Node, physical or virtual, is represented by a set of input and output variables which can be accessed by any other nodes in the system, and each runs continuously in its own thread. Input variables are simply variables in the memory that Nodes have read access to. Similarly, output variables are variables that Nodes have write access to. Multiple Nodes can share one input variable while only one Node can be associated with one output variable. 

At the lowest level, Input Nodes continuously update their associated variables, and Output Nodes continuously send output requests to InteractiveCmd through the Messenger. Different types of Input and Output nodes are configured to run at a loop period compatible with the physical components that they represent. This mechanism makes implementation of the higher level Nodes much easier by eliminating the need for communicating with the InteractiveCmd by means of sending individual messages. Instead, each of the input and output variables can be accessed from the memory at any time. These variables are used as building blocks for higher level Nodes. In addition, intermediate level Nodes can embed extra functionalities. For instance, a LED Driver ramps up or dims an LED to the desired brightness level. A higher-level Node controlling that LED using the LED Driver can then operate at a lower update period and process more complex logic. This Node Abstraction system makes developing CBLA Nodes much simpler by eliminating the need for managing logic requiring different frequencies of control under one thread. 

The addition of the Messenger node between the InteractiveCmd, and Input and Output Nodes streamlines the communication by reducing the number of messages. Over USB, each packet can contain up to 64 bytes. If each Node communicates with the InteractiveCmd directly, there will be many messages that might only require one or two bytes. A large portion of the communication bandwidth will be wasted and the update rate of the Nodes will be significantly throttled. Since many messages are likely to be delivered to the same Teensy, those messages can be combined and delivered as a single packet. The job of the Messenger Node is to collect all the messages, combine them appropriately, and deliver them to the InteractiveCmd periodically. Although this means that each message must wait for the next delivery cycle to be sent out, this mechanism allows the system to handle a much higher throughput. To avoid commands or requests being missed, the rate of each Input or Output node is set to be at least three times the Messenger's update period. 

Initializing the Teensy Interfaces
----------------------------------------

The Teensy Interface is part of the *interactive-system*. Therefoe, one must first import interactive_system.

>>> import interactive_system

Teensy Interface are created by instantiating the Teensy Manager. It will search for all the Teensy devices that are connected and instantiate a Teensy Interface thread for each Teensy device.

>>> teensy_manager = interactive_system.TeensyManager(import_config=True, protocols_dict=protocols)

If *import_config* is true, in the directory where the program executes, a directory named *protocol_variables* must be created. In it, two files that list out the input and output variables and their properites respectively must be created. Otherwise, only the default set of input nad output variables would be created. Each pair of file correspond to a particular protocol.

In addition, a dictionary of protocol should also be pased to the *protocol_dict* parameter. Each protocol extends *interactive_system.SystemParameter*. 

Moreover, a file named *teensy_config* must be created in the directory where the program executes.  It assigns names and their corresponding protocol to Teensy devices based on their Serial Number.

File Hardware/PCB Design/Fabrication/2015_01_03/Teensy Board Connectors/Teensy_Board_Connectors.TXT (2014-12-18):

%
M48
M72
T01C0.0236
T02C0.0354
T03C0.0400
T04C0.1280
%
T01
X10160Y4283
X11660Y7383
X12460Y7383
X13260Y7383
X14060Y7383
X15860Y7283
X16660Y7283
X17460Y7283
X18260Y7283
X18460Y9983
X19160Y12283
X18260Y15083
X17460Y15083
X16660Y15083
X15860Y15083
X14060Y14883
X13260Y14883
X12460Y14883
X11660Y14883
X18660Y18883
X19160Y21283
X17560Y22883
X16960Y22883
X16160Y22883
X15360Y22883
X14060Y23083
X13260Y23083
X12460Y23083
X11660Y23083
X22160Y5283
X19160Y4283
X19160Y4283
X18760Y1983
T02
X25260Y3033
X26260Y3533
X25260Y4033
X26260Y4533
X25260Y5033
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

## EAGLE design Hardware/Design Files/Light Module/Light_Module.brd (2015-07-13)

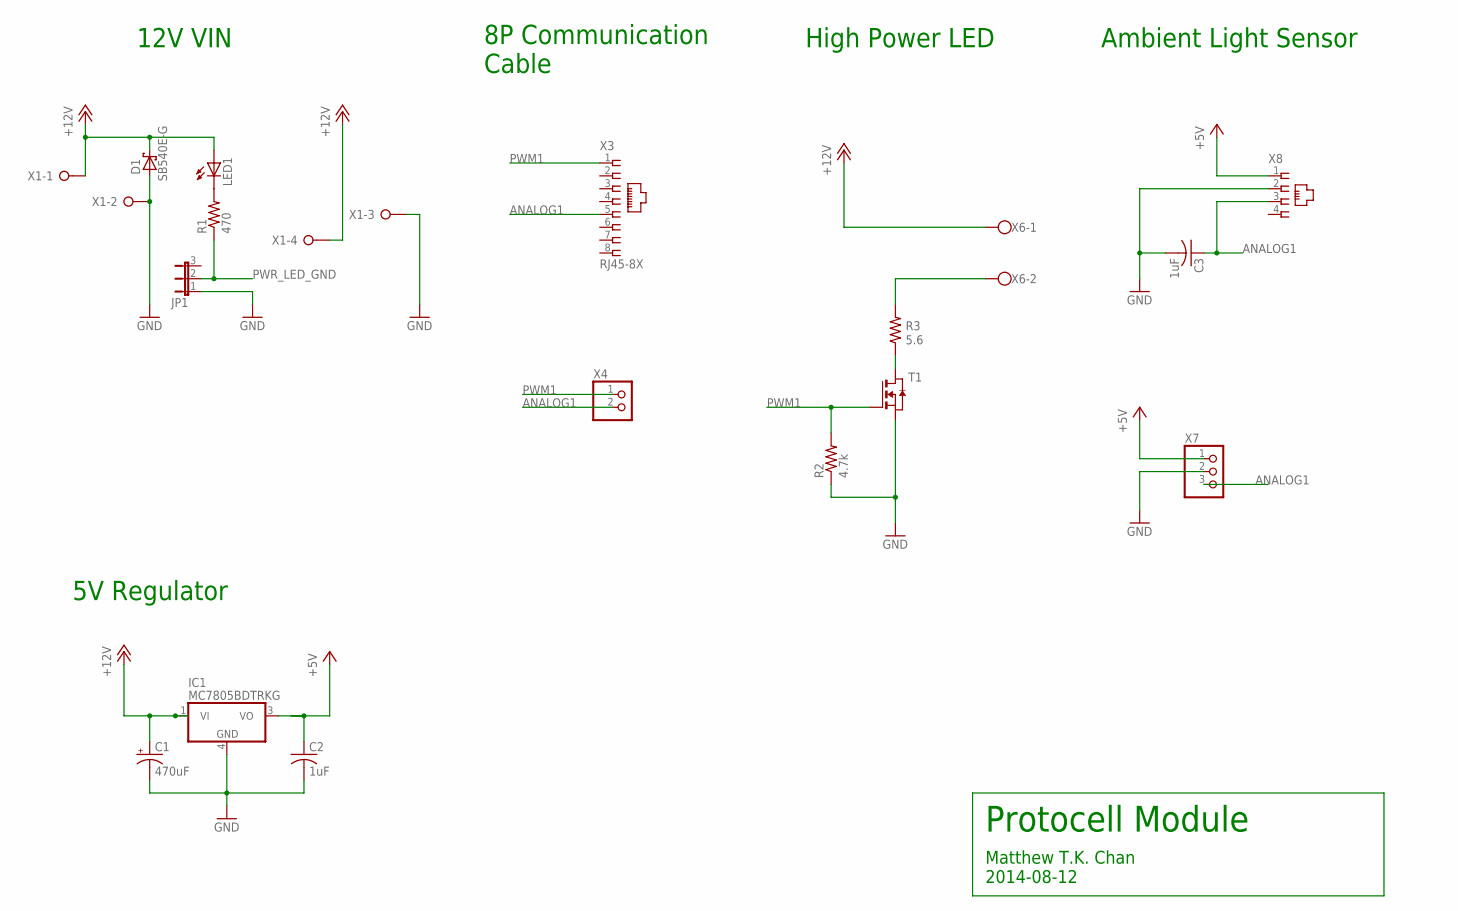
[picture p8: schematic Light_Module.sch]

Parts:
C1: 470uF; E5-10,5
C2, C3: 1uF; C0603
D1: SB540E-G; DO201T15
IC1: MC7805BDTRKG; DPACK_3
JP1: JP2E; JP2
LED1: LEDSML1206; SML1206
R1: 470; R0603
R2: 4.7k; R0603
R3: 5.6; YAGEO_SQP500JB
T1: NTD5867NLT4G; DPACK
X1: W237-04P; W237-4P
X3: RJ45-8X; RJ45-NO-SHIELD
X4: PINHD-1X2; 1X02
X6: W237-102
X7: PINHD-1X3; 1X03
X8: 558872-1

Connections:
+5V: C2.1, IC1.3 (VO), X7.1, X8.1
+12V: C1.+, D1.C, IC1.1 (VI), LED1.A, X1.1, X1.4, X6.1
ANALOG1: C3.1, X3.5, X4.2, X7.3, X8.3
GND: C1.-, C2.2, C3.2, D1.A, IC1.4 (GND), JP1.1, R2.1, T1.3 (S), X1.2, X1.3, X7.2, X8.2
unnamed: R3.1, T1.2 (D)
unnamed: R3.2, X6.2
unnamed: LED1.C, R1.2
PWM1: R2.2, T1.1 (G), X3.1, X4.1
PWR_LED_GND: JP1.2, R1.1

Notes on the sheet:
Protocell Module
Matthew T.K. Chan 2014-08-12
High Power LED
Ambient Light Sensor
12V VIN
5V Regulator
8P Communication Cable

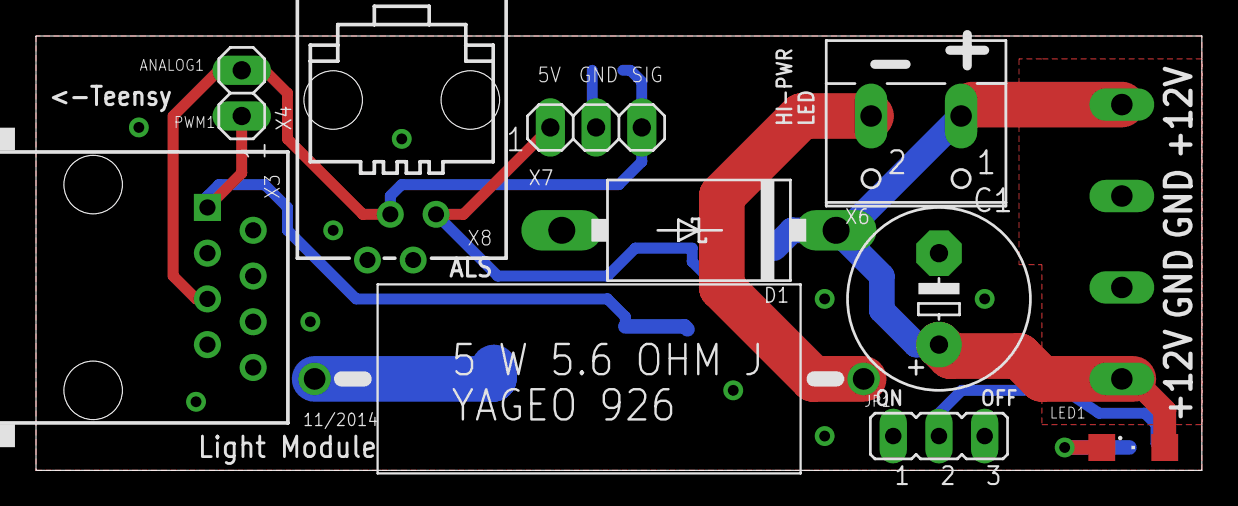
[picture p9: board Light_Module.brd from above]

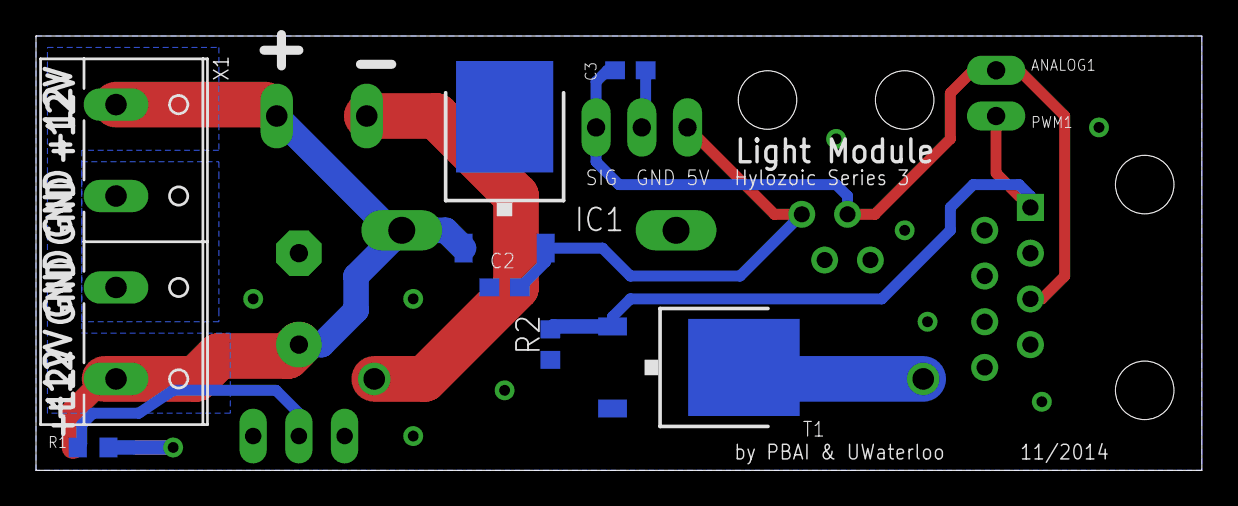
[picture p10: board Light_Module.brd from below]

Board: 2 copper layers, 64.8 x 24.1 mm, 17 parts (7 on the bottom side), 9 nets.

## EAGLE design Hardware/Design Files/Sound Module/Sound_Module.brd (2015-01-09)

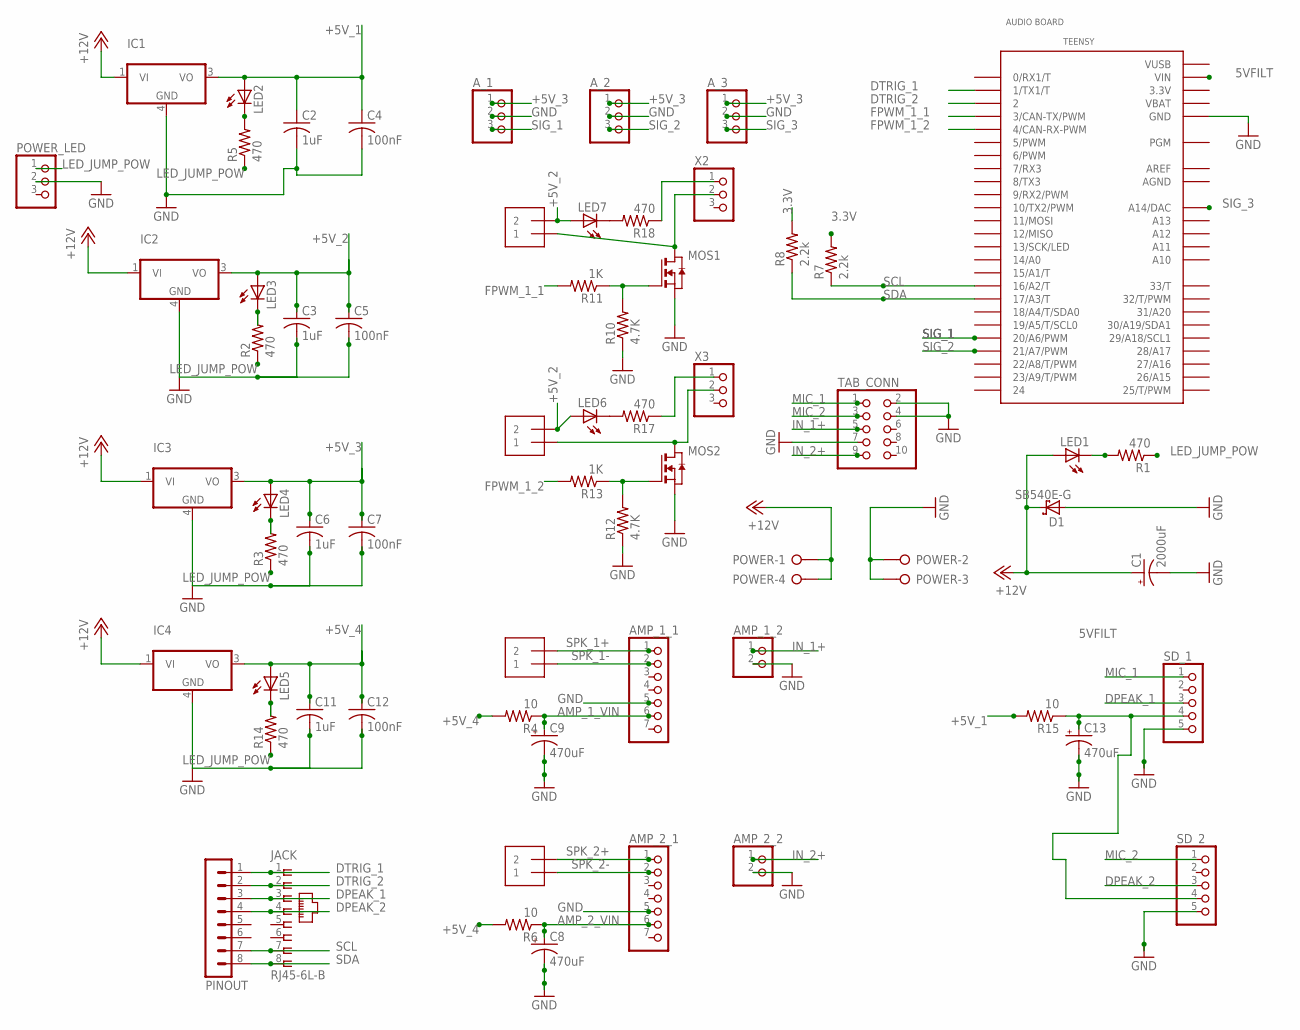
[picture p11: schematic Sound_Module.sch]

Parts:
AMP_1_1, AMP_2_1: PINHD-1X7; 1X07
AMP_1_2, AMP_2_2: PINHD-1X2; 1X02
A_1, A_2, A_3: PINHD-1X3; 1X03
C1: 2000uF; E5-10,5
C2, C3, C6, C11: 1uF; C0603
C4, C5, C7, C12: 100nF; C0603
C8, C9, C13: 470uF; E5-10,5
D1: SB540E-G; DO201T15
IC1, IC2, IC3, IC4: MC7805BDTRKG; DPACK_3
JACK: RJ45-6L-B; RJ45-NO-SHIELD
LED1, LED2, LED3, LED4, LED5, LED6, LED7: LEDSML1206; SML1206
MOS1, MOS2: NTD5867NLT4G; DPACK
PINOUT: MA08-1
POWER: W237-04P; W237-4P
POWER_LED: PINHD-1X3; 1X03
PWM1, PWM2: 1X2-3.5MM
R1, R2, R3, R5, R14, R17, R18: 470; R0603
R4, R6, R15: 10; R0603
R7, R8: 2.2k; R0603
R10, R12: 4.7K; R0603
R11, R13: 1K; R0603
SD_1, SD_2: PINHD-1X5; 1X05
SPK-1, SPK-2: 1X2-3.5MM
TAB_CONN: PINHD-2X5; 2X05
TEENSY: AUDIO BOARD; TEENSY_3.1_ALLPINS
X2, X3: PINHD-1X3; 1X03

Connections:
3.3V: R7.2, R8.2, TEENSY.3.3V, TEENSY.3.3V1 (3.3V), TEENSY.3.3V2 (3.3V)
5VFILT: C13.+, R15.1, SD_1.4, SD_2.4, TEENSY.VIN
+5V_1: C2.1, C4.1, IC1.3 (VO), LED2.A, R15.2
+5V_2: C3.1, C5.1, IC2.3 (VO), LED3.A, LED6.A, LED7.A, PWM1.2, PWM2.2
+5V_3: A_1.1, A_2.1, A_3.1, C6.1, C7.1, IC3.3 (VO), LED4.A
+5V_4: C11.1, C12.1, IC4.3 (VO), LED5.A, R4.2, R6.2
+12V: C1.+, D1.C, IC1.1 (VI), IC2.1 (VI), IC3.1 (VI), IC4.1 (VI), LED1.A, POWER.1, POWER.4
AGND: TEENSY.AGND
AMP_1_VIN: AMP_1_1.6, C9.+, R4.1
AMP_2_VIN: AMP_2_1.6, C8.+, R6.1
AREF: TEENSY.AREF
DPEAK_1: JACK.3, PINOUT.3, SD_1.3
DPEAK_2: JACK.4, PINOUT.4, SD_2.3
DTRIG_1: JACK.1, PINOUT.1, TEENSY.1 (1/TX1/T)
DTRIG_2: JACK.2, PINOUT.2, TEENSY.2
FPWM_1_1: R11.2, TEENSY.3 (3/CAN-TX/PWM)
FPWM_1_2: R13.2, TEENSY.4 (4/CAN-RX-PWM)
GND: AMP_1_1.5, AMP_1_2.2, AMP_2_1.5, AMP_2_2.2, A_1.2, A_2.2, A_3.2, C1.-, C2.2, C3.2, C4.2, C5.2, C6.2, C7.2, C8.-, C9.-, C11.2, C12.2, C13.-, D1.A, IC1.4 (GND), IC2.4 (GND), IC3.4 (GND), IC4.4 (GND), MOS1.3 (S), MOS2.3 (S), POWER.2, POWER.3, POWER_LED.2, R10.1, R12.1, SD_1.5, SD_2.5, TAB_CONN.2, TAB_CONN.4, TAB_CONN.7, TEENSY.GND, TEENSY.GND1 (GND), TEENSY.GND2 (GND)
IN_1+: AMP_1_2.1, TAB_CONN.5
IN_2+: AMP_2_2.1, TAB_CONN.9
LED_JUMP_POW: POWER_LED.1, R1.1, R2.1, R3.1, R5.1, R14.1
MIC_1: SD_1.1, TAB_CONN.1
MIC_2: SD_2.1, TAB_CONN.3
unnamed: MOS2.1 (G), R12.2, R13.1
unnamed: LED3.C, R2.2
unnamed: LED4.C, R3.2
unnamed: MOS1.1 (G), R10.2, R11.1
unnamed: MOS1.2 (D), PWM1.1, X2.2
unnamed: LED6.C, R17.2
unnamed: MOS2.2 (D), PWM2.1, X3.2
unnamed: LED5.C, R14.2
unnamed: LED7.C, R18.2
unnamed: LED1.C, R1.2
unnamed: R18.1, X2.1
unnamed: R17.1, X3.1
unnamed: LED2.C, R5.2
SCL: JACK.7, PINOUT.7, R7.1, TEENSY.16/A2 (16/A2/T)
SDA: JACK.8, PINOUT.8, R8.1, TEENSY.17/A3 (17/A3/T)
SIG_1: A_1.3, TEENSY.20/A6 (20/A6/PWM)
SIG_2: A_2.3, TEENSY.21/A7 (21/A7/PWM)
SIG_3: A_3.3, TEENSY.A14 (A14/DAC)
SPK_1+: AMP_1_1.1, SPK-1.2
SPK_1-: AMP_1_1.2, SPK-1.1
SPK_2+: AMP_2_1.1, SPK-2.2
SPK_2-: AMP_2_1.2, SPK-2.1
VBAT: TEENSY.VBAT
VUSB: TEENSY.VUSB

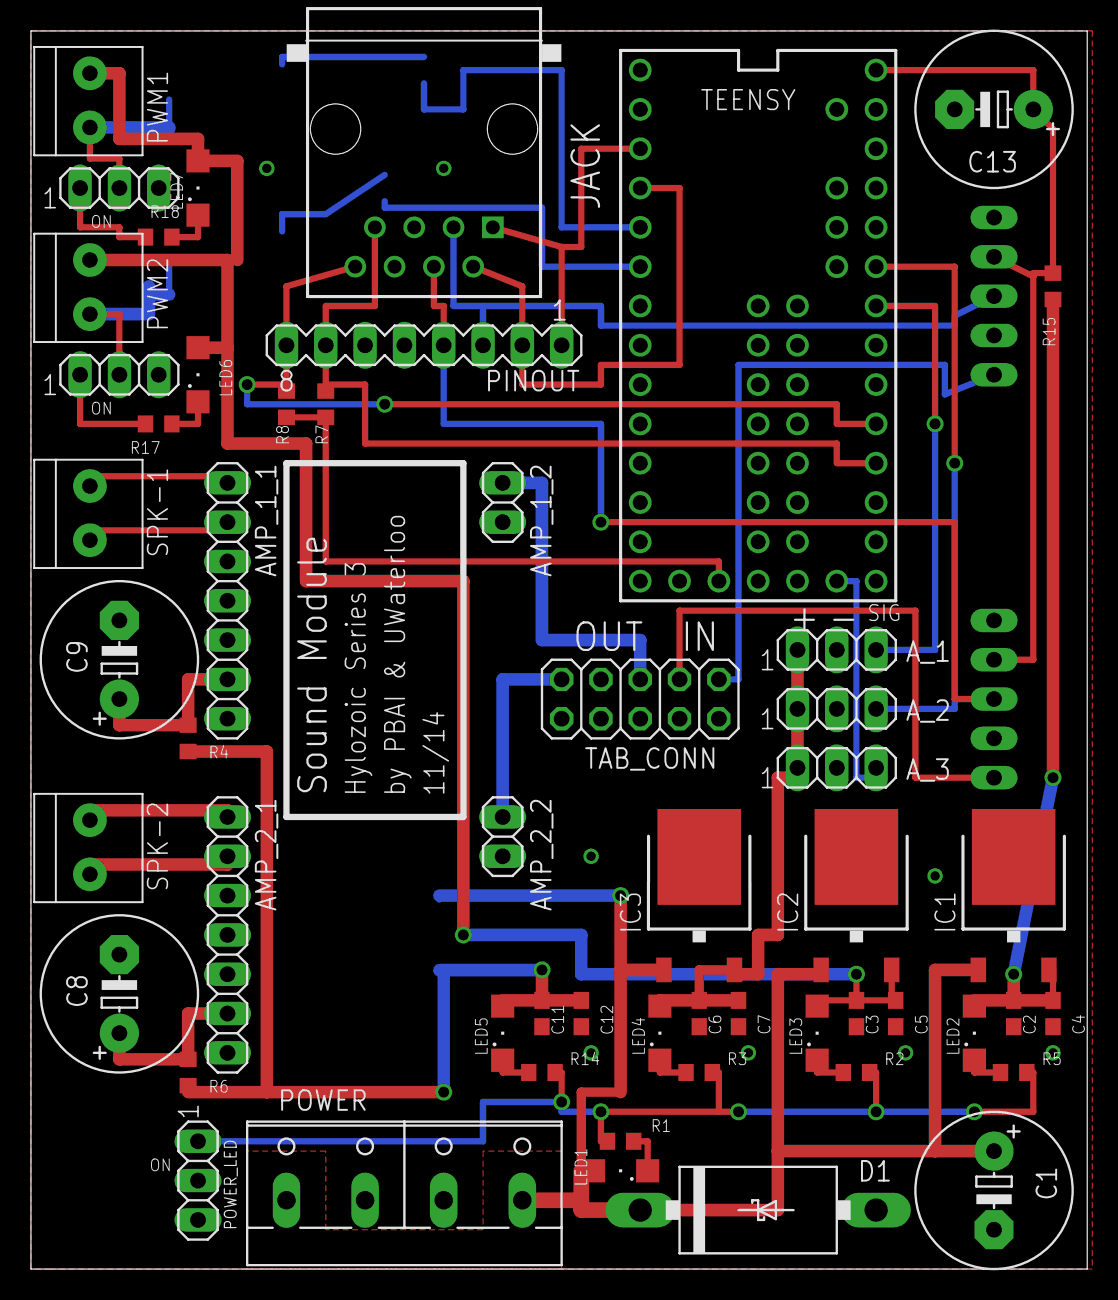
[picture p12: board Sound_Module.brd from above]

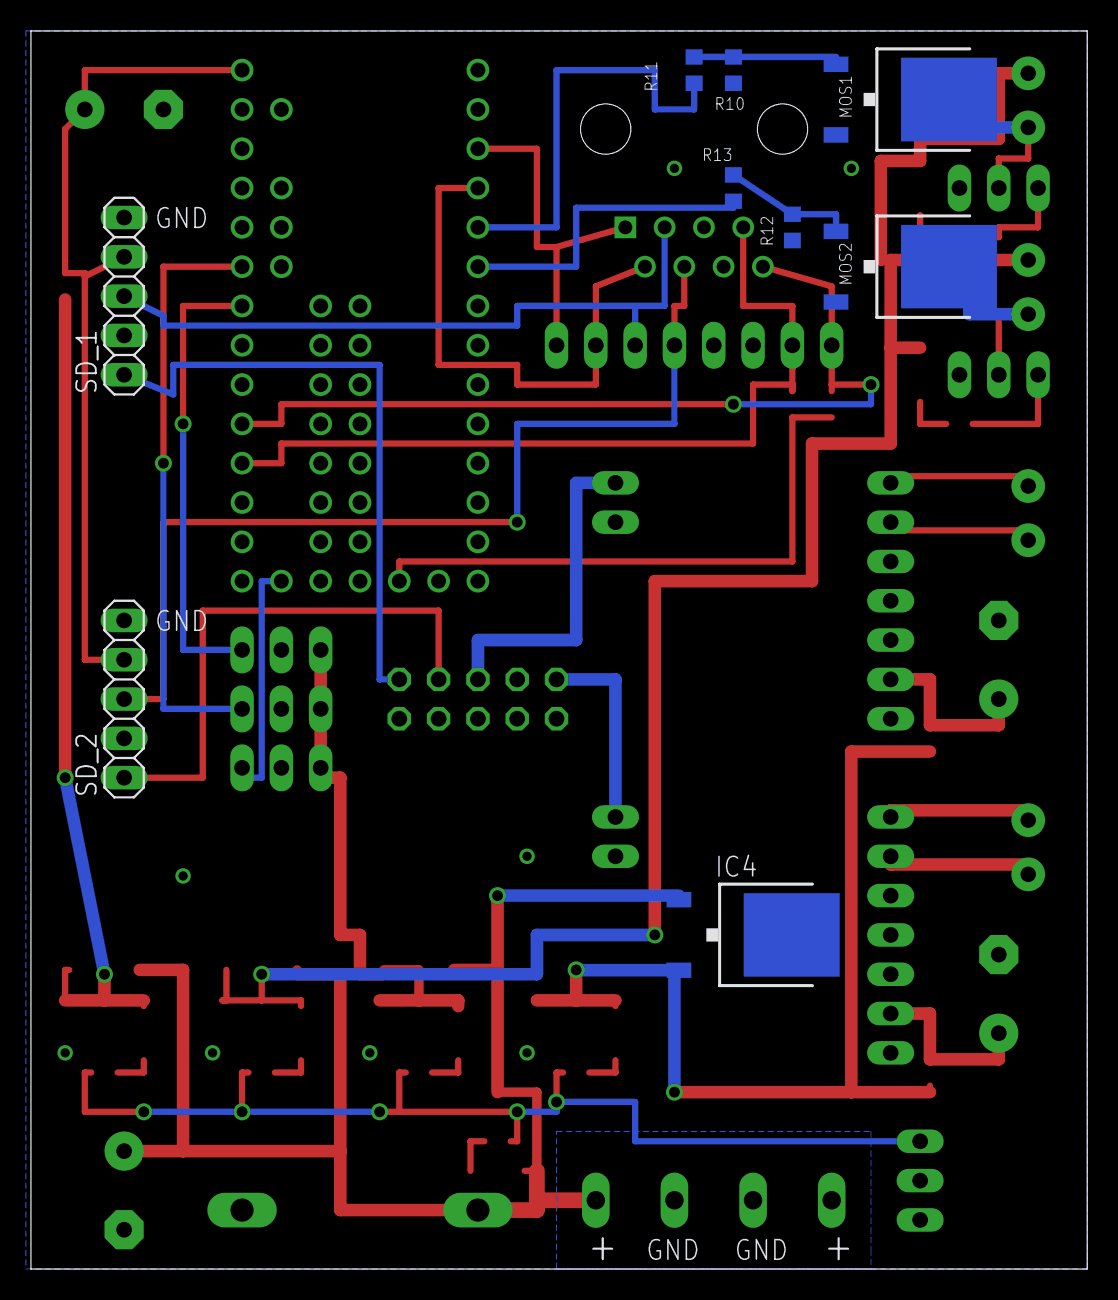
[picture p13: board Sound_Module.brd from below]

Board: 2 copper layers, 68.2 x 80.0 mm, 63 parts (9 on the bottom side), 43 nets.

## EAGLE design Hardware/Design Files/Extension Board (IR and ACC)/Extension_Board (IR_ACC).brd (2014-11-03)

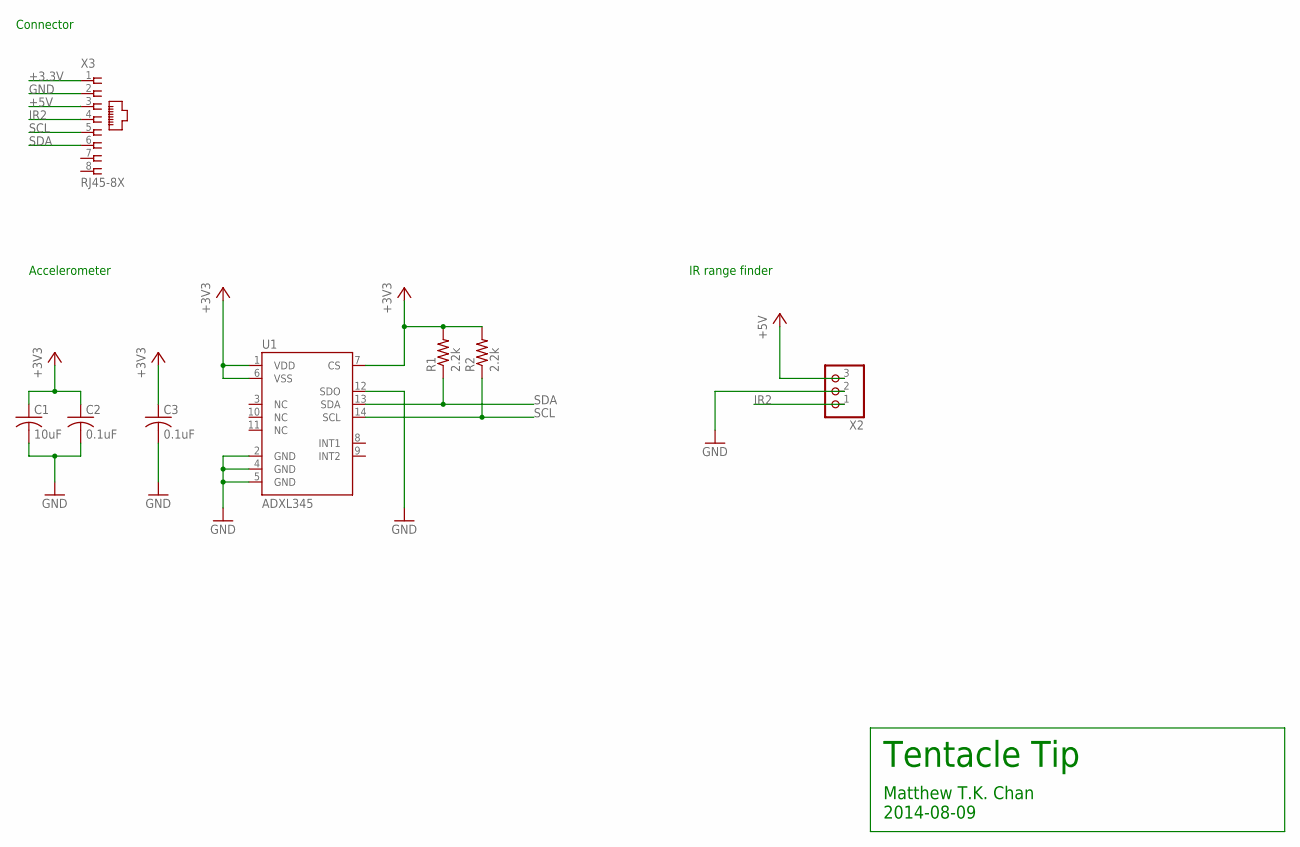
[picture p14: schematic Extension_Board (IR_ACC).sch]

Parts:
C1: 10uF; C1206
C2, C3: 0.1uF; C0603
R1, R2: 2.2k; R0603
U1: ADXL345; LGA14_LONG
X2: PINHD-1X3/90; 1X03/90
X3: RJ45-8X; RJ45-NO-SHIELD

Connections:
+3.3V: C1.1, C2.1, C3.1, R1.2, R2.2, U1.1 (VDD), U1.6 (VSS), U1.7 (CS), X3.1
+5V: X2.3, X3.3
GND: C1.2, C2.2, C3.2, U1.2 (GND), U1.4 (GND), U1.5 (GND), U1.12 (SDO), X2.2, X3.2
IR2: X2.1, X3.4
SCL: R2.1, U1.14 (SCL), X3.5
SDA: R1.1, U1.13 (SDA), X3.6

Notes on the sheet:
Tentacle Tip
Matthew T.K. Chan 2014-08-09
Accelerometer
IR range finder
Connector

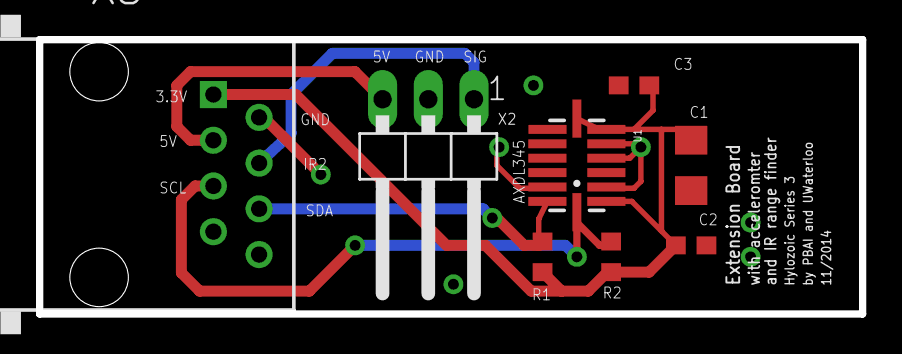
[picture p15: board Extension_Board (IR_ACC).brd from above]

Board: 2 copper layers, 45.7 x 15.2 mm, 8 parts (0 on the bottom side), 6 nets.

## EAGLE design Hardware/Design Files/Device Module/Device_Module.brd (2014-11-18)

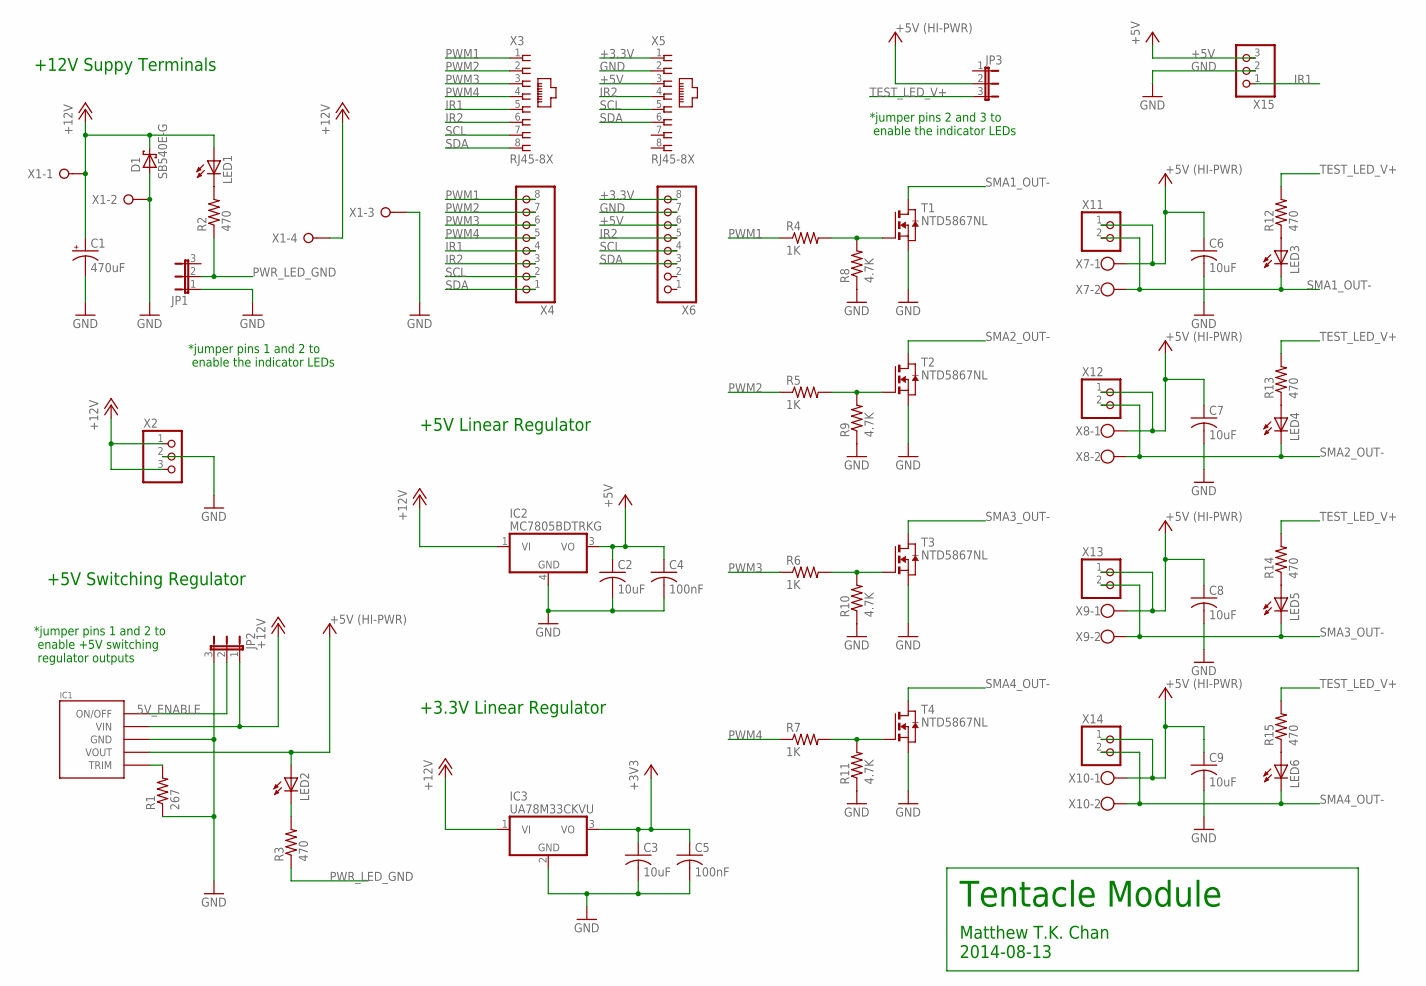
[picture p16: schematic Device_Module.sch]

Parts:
C1: 470uF; E5-10,5
C2, C3, C6, C7, C8, C9: 10uF; C1206
C4, C5: 100nF; C0603
D1: SB540E-G; DO201T15
IC1: OKR-T/10-W12; OKR-C90
IC2: MC7805BDTRKG; DPACK_3
IC3: UA78M33CKVU; DPACK
JP1, JP2, JP3: JP2E; JP2
LED1, LED2, LED3, LED4, LED5, LED6: LEDSML1206; SML1206
R1: 267; R0603
R2, R3, R12, R13, R14, R15: 470; R0603
R4, R5, R6, R7: 1K; R0603
R8, R9, R10, R11: 4.7K; R0603
T1, T2, T3, T4: NTD5867NL; DPACK
X1: W237-04P; W237-4P
X2, X15: PINHD-1X3/90; 1X03/90
X3, X5: RJ45-8X; RJ45-NO-SHIELD
X4, X6: PINHD-1X8; 1X08
X7, X8, X9, X10: W237-102
X11, X12, X13, X14: PINHD-1X2/90; 1X02/90

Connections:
5V_ENABLE: IC1.ON/OFF, JP2.2
+3.3V: C3.1, C5.1, IC3.3 (VO), X5.1, X6.8
+5V: C2.1, C4.1, IC2.3 (VO), X5.3, X6.6, X15.3
+5V_HI-PWR: C6.1, C7.1, C8.1, C9.1, IC1.VOUT, JP3.2, LED2.A, X7.1, X8.1, X9.1, X10.1, X11.1, X12.1, X13.1, X14.1
+12V: C1.+, D1.C, IC1.VIN, IC2.1 (VI), IC3.1 (VI), JP2.1, LED1.A, X1.1, X1.4, X2.1, X2.3
GND: C1.-, C2.2, C3.2, C4.2, C5.2, C6.2, C7.2, C8.2, C9.2, D1.A, IC1.GND, IC2.4 (GND), IC3.2 (GND), JP1.1, JP2.3, R1.1, R8.1, R9.1, R10.1, R11.1, T1.3 (S), T2.3 (S), T3.3 (S), T4.3 (S), X1.2, X1.3, X2.2, X5.2, X6.7, X15.2
IR1: X3.5, X4.4, X15.1
IR2: X3.6, X4.3, X5.4, X6.5
unnamed: R5.2, R9.2, T2.1 (G)
unnamed: R6.2, R10.2, T3.1 (G)
unnamed: R7.2, R11.2, T4.1 (G)
unnamed: R4.2, R8.2, T1.1 (G)
unnamed: LED3.A, R12.1
unnamed: IC1.TRIM, R1.2
unnamed: LED2.C, R3.2
unnamed: LED1.C, R2.2
unnamed: LED4.A, R13.1
unnamed: LED5.A, R14.1
unnamed: LED6.A, R15.1
PWM1: R4.1, X3.1, X4.8
PWM2: R5.1, X3.2, X4.7
PWM3: R6.1, X3.3, X4.6
PWM4: R7.1, X3.4, X4.5
PWR_LED_GND: JP1.2, R2.1, R3.1
SCL: X3.7, X4.2, X5.5, X6.4
SDA: X3.8, X4.1, X5.6, X6.3
SMA1_OUT-: LED3.C, T1.2 (D), X7.2, X11.2
SMA2_OUT-: LED4.C, T2.2 (D), X8.2, X12.2
SMA3_OUT-: LED5.C, T3.2 (D), X9.2, X13.2
SMA4_OUT-: LED6.C, T4.2 (D), X10.2, X14.2
TEST_LED_V+: JP3.3, R12.2, R13.2, R14.2, R15.2

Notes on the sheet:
Tentacle Module
Matthew T.K. Chan 2014-08-13
+12V Suppy Terminals
*jumper pins 2 and 3 to enable the indicator LEDs
+5V Switching Regulator
*jumper pins 1 and 2 to enable the indicator LEDs
*jumper pins 1 and 2 to enable +5V switching regulator outputs
+5V Linear Regulator
+3.3V Linear Regulator

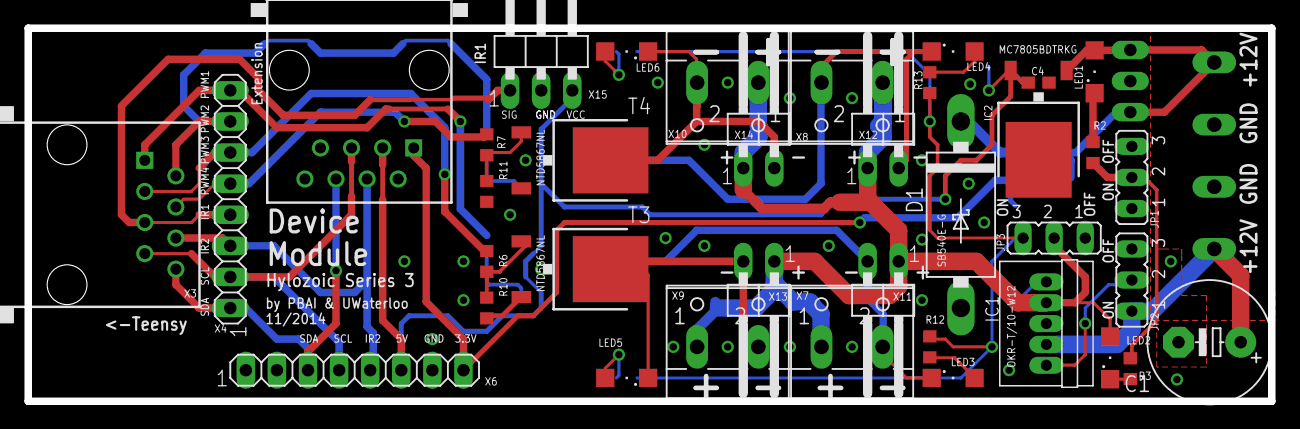
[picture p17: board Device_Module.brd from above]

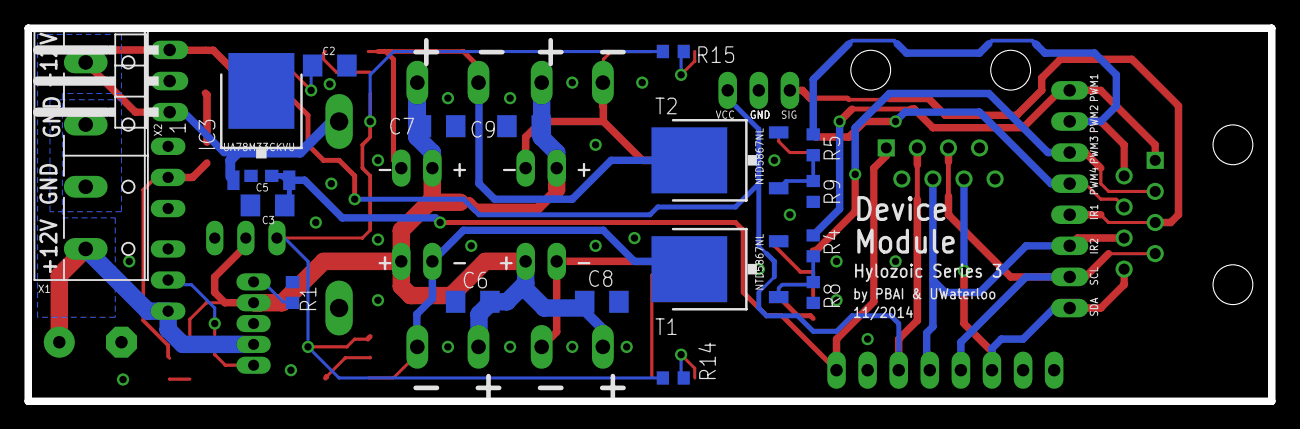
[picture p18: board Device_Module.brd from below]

Board: 2 copper layers, 101.6 x 30.5 mm, 56 parts (19 on the bottom side), 31 nets.

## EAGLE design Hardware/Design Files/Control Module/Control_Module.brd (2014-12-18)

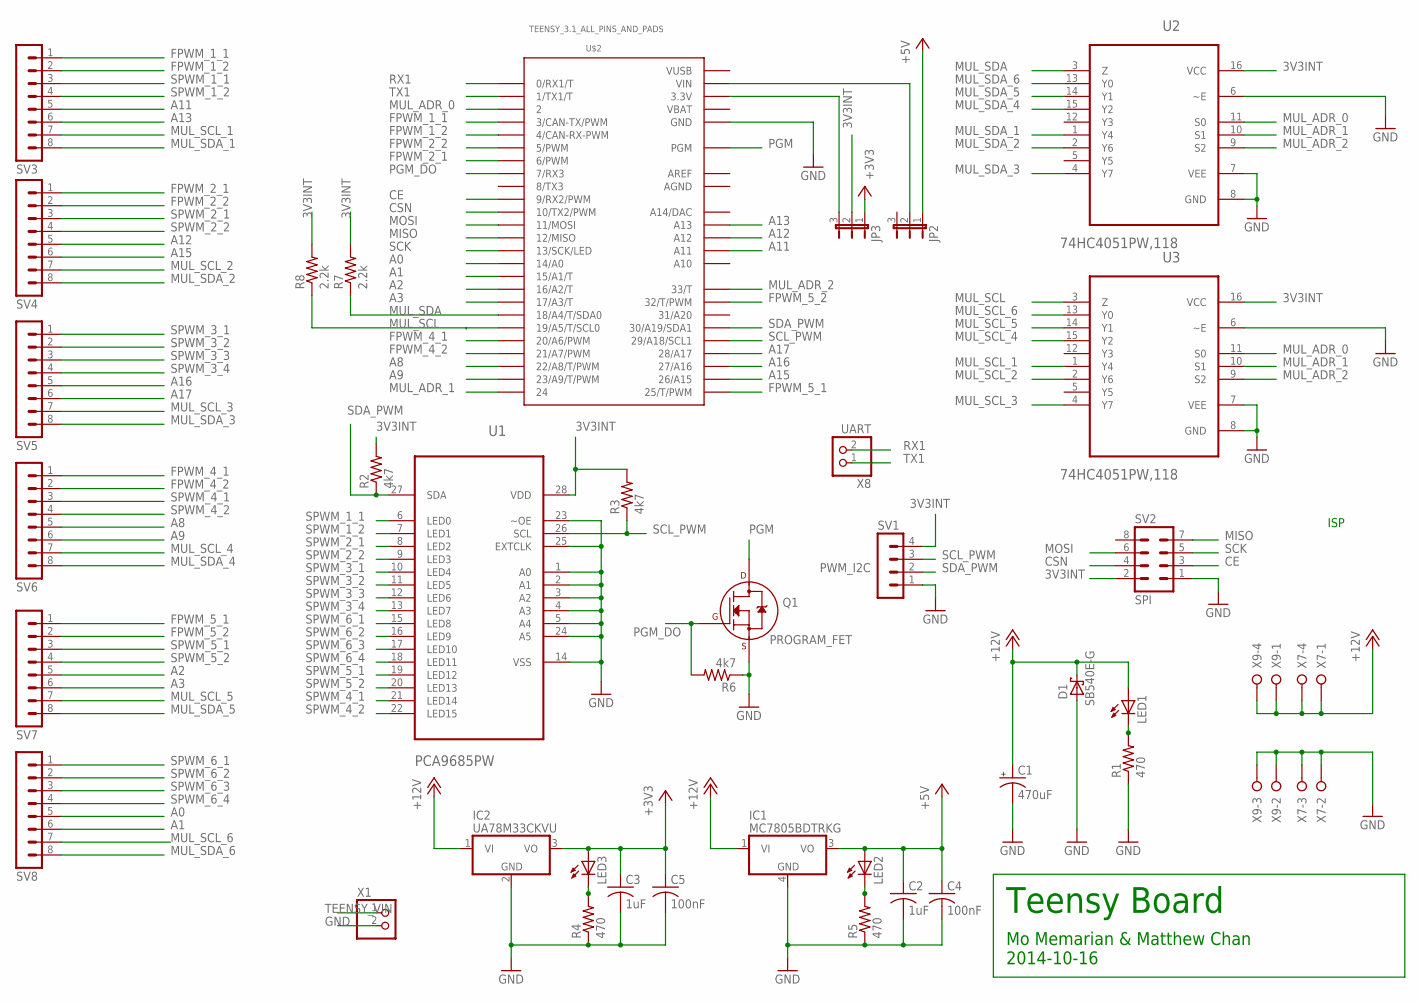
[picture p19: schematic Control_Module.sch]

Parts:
C1: 470uF; E5-10,5
C2, C3: 1uF; C0603
C4, C5: 100nF; C0603
D1: SB540E-G; DO201T15
IC1: MC7805BDTRKG; DPACK_3
IC2: UA78M33CKVU; DPACK
JP2, JP3: JP2E; JP2
LED1, LED2, LED3: LEDSML1206; SML1206
Q1: PROGRAM_FET; SOT-23
R1, R4, R5: 470; R0603
R2, R3, R6: 4k7; R0603
R7, R8: 2.2k; R0603
SV1: PWM_I2C; MA04-1
SV2: SPI; MA04-2
SV3, SV4, SV5, SV6, SV7, SV8: MA08-1
U1: PCA9685PW; SOP65P640X110-28N
U2, U3: 74HC4051PW,118; SOP65P640X110-16N
U$2: TEENSY_3.1_ALL_PINS_AND_PADS; TEENSY_3.1_ALLPINS
X1: PINHD-1X2; 1X02
X7, X9: W237-04P; W237-4P
X8: UART; 1X02

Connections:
3V3INT: JP3.2, R2.2, R3.2, R7.2, R8.2, SV1.4, SV2.2, U1.28 (VDD), U2.16 (VCC), U3.16 (VCC)
+3V3: C3.1, C5.1, IC2.3 (VO), JP3.1, LED3.A
+5V: C2.1, C4.1, IC1.3 (VO), JP2.1, LED2.A
+12V: C1.+, D1.C, IC1.1 (VI), IC2.1 (VI), LED1.A, X7.1, X7.4, X9.1, X9.4
A0: SV8.5, U$2.14/A0
A1: SV8.6, U$2.15/A1 (15/A1/T)
A2: SV7.5, U$2.16/A2 (16/A2/T)
A3: SV7.6, U$2.17/A3 (17/A3/T)
A8: SV6.5, U$2.22/A8 (22/A8/T/PWM)
A9: SV6.6, U$2.23/A9 (23/A9/T/PWM)
A11: SV3.5, U$2.A11
A12: SV4.5, U$2.A12
A13: SV3.6, U$2.A13
A15: SV4.6, U$2.26 (26/A15)
A16: SV5.5, U$2.27 (27/A16)
A17: SV5.6, U$2.28 (28/A17)
AGND: U$2.AGND
AREF: U$2.AREF
CE: SV2.3, U$2.9 (9/RX2/PWM)
CSN: SV2.4, U$2.10 (10/TX2/PWM)
FPWM_1_1: SV3.1, U$2.3 (3/CAN-TX/PWM)
FPWM_1_2: SV3.2, U$2.4 (4/CAN-RX-PWM)
FPWM_2_1: SV4.1, U$2.6 (6/PWM)
FPWM_2_2: SV4.2, U$2.5 (5/PWM)
FPWM_4_1: SV6.1, U$2.20/A6 (20/A6/PWM)
FPWM_4_2: SV6.2, U$2.21/A7 (21/A7/PWM)
FPWM_5_1: SV7.1, U$2.25 (25/T/PWM)
FPWM_5_2: SV7.2, U$2.32 (32/T/PWM)
GND: C1.-, C2.2, C3.2, C4.2, C5.2, D1.A, IC1.4 (GND), IC2.2 (GND), Q1.2 (S), R1.1, R4.1, R5.1, R6.1, SV1.1, SV2.1, U1.1 (A0), U1.2 (A1), U1.3 (A2), U1.4 (A3), U1.5 (A4), U1.14 (VSS), U1.23 (~OE), U1.24 (A5), U1.25 (EXTCLK), U2.6 (~E), U2.7 (VEE), U2.8 (GND), U3.6 (~E), U3.7 (VEE), U3.8 (GND), U$2.GND, U$2.GND1 (GND), U$2.GND2 (GND), X1.2, X7.2, X7.3, X9.2, X9.3
MISO: SV2.7, U$2.12 (12/MISO)
MOSI: SV2.6, U$2.11 (11/MOSI)
MUL_ADR_0: U2.11 (S0), U3.11 (S0), U$2.2
MUL_ADR_1: U2.10 (S1), U3.10 (S1), U$2.24
MUL_ADR_2: U2.9 (S2), U3.9 (S2), U$2.33 (33/T)
MUL_SCL: R8.1, U3.3 (Z), U$2.19/A5 (19/A5/T/SCL0)
MUL_SCL_1: SV3.7, U3.1 (Y4)
MUL_SCL_2: SV4.7, U3.2 (Y6)
MUL_SCL_3: SV5.7, U3.4 (Y7)
MUL_SCL_4: SV6.7, U3.15 (Y2)
MUL_SCL_5: SV7.7, U3.14 (Y1)
MUL_SCL_6: SV8.7, U3.13 (Y0)
MUL_SDA: R7.1, U2.3 (Z), U$2.18/A4 (18/A4/T/SDA0)
MUL_SDA_1: SV3.8, U2.1 (Y4)
MUL_SDA_2: SV4.8, U2.2 (Y6)
MUL_SDA_3: SV5.8, U2.4 (Y7)
MUL_SDA_4: SV6.8, U2.15 (Y2)
MUL_SDA_5: SV7.8, U2.14 (Y1)
MUL_SDA_6: SV8.8, U2.13 (Y0)
unnamed: LED1.C, R1.2
unnamed: LED3.C, R4.2
unnamed: LED2.C, R5.2
PGM: Q1.3 (D), U$2.PGM
PGM_DO: Q1.1 (G), R6.2, U$2.7 (7/RX3)
RX1: U$2.0 (0/RX1/T), X8.2
SCK: SV2.5, U$2.13 (13/SCK/LED)
SCL_PWM: R3.1, SV1.3, U1.26 (SCL), U$2.29 (29/A18/SCL1)
SDA_PWM: R2.1, SV1.2, U1.27 (SDA), U$2.30 (30/A19/SDA1)
SPWM_1_1: SV3.3, U1.6 (LED0)
SPWM_1_2: SV3.4, U1.7 (LED1)
SPWM_2_1: SV4.3, U1.8 (LED2)
SPWM_2_2: SV4.4, U1.9 (LED3)
SPWM_3_1: SV5.1, U1.10 (LED4)
SPWM_3_2: SV5.2, U1.11 (LED5)
SPWM_3_3: SV5.3, U1.12 (LED6)
SPWM_3_4: SV5.4, U1.13 (LED7)
SPWM_4_1: SV6.3, U1.21 (LED14)
SPWM_4_2: SV6.4, U1.22 (LED15)
SPWM_5_1: SV7.3, U1.19 (LED12)
SPWM_5_2: SV7.4, U1.20 (LED13)
SPWM_6_1: SV8.1, U1.15 (LED8)
SPWM_6_2: SV8.2, U1.16 (LED9)
SPWM_6_3: SV8.3, U1.17 (LED10)
SPWM_6_4: SV8.4, U1.18 (LED11)
TEENSY_3V3: JP3.3, U$2.3.3V, U$2.3.3V1 (3.3V), U$2.3.3V2 (3.3V)
TEENSY_VIN: JP2.2, U$2.VIN, X1.1
TX1: U$2.1 (1/TX1/T), X8.1
VBAT: U$2.VBAT
VUSB: U$2.VUSB

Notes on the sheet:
Teensy Board
Mo Memarian & Matthew Chan 2014-10-16
ISP



Board: 2 copper layers, 75.7 x 80.8 mm, 38 parts (7 on the bottom side), 74 nets.

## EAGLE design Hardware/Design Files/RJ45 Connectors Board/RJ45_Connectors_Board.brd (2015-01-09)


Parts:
IC1, IC2, IC3: ULN2803AFWG; SOP18
LED1, LED2, LED3, LED4, LED5, LED6, LED7, LED8, LED9, LED10, LED11, LED12, LED13, LED14, LED15, LED16, LED17, LED18, LED19, LED20, LED21, LED22, LED23, LED24: LEDSML1206; SML1206
R1, R2, R3, R4, R5, R6, R7, R8, R9, R10, R11, R12, R13, R14, R15, R16, R17, R18, R19, R20, R21, R22, R23, R24: 470; R0603
SV1, SV2, SV9, SV10, SV11, SV12: MA08-1
SV3, SV4, SV5, SV6, SV7, SV8: RJ45-8X; RJ45-NO-SHIELD
X1: PINHD-1X2; 1X02
X2: PINHD-1X3; 1X03

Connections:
+5V: IC1.10 (CD+), IC2.10 (CD+), IC3.10 (CD+), LED1.A, LED2.A, LED3.A, LED4.A, LED5.A, LED6.A, LED7.A, LED8.A, LED9.A, LED10.A, LED11.A, LED12.A, LED13.A, LED14.A, LED15.A, LED16.A, LED17.A, LED18.A, LED19.A, LED20.A, LED21.A, LED22.A, LED23.A, LED24.A, X2.2
+5VJUMP: X1.1, X2.1
A0: SV8.5, SV12.5
A1: SV8.6, SV12.6
A2: SV7.5, SV11.5
A3: SV7.6, SV11.6
A8: SV6.5, SV10.5
A9: SV6.6, SV10.6
A11: SV1.5, SV3.5
A12: SV2.5, SV4.5
A13: SV1.6, SV3.6
A15: SV2.6, SV4.6
A16: SV5.5, SV9.5
A17: SV5.6, SV9.6
FPWM_1_1: IC1.1 (I1), SV1.1, SV3.1
FPWM_1_2: IC1.2 (I2), SV1.2, SV3.2
FPWM_2_1: IC2.1 (I1), SV2.1, SV4.1
FPWM_2_2: IC2.2 (I2), SV2.2, SV4.2
FPWM_4_1: IC1.5 (I5), SV6.1, SV10.1
FPWM_4_2: IC1.6 (I6), SV6.2, SV10.2
FPWM_5_1: IC2.5 (I5), SV7.1, SV11.1
FPWM_5_2: IC2.6 (I6), SV7.2, SV11.2
GND: IC1.9 (GND), IC2.9 (GND), IC3.9 (GND), X1.2
MUL_SCL_1: SV1.7, SV3.7
MUL_SCL_2: SV2.7, SV4.7
MUL_SCL_3: SV5.7, SV9.7
MUL_SCL_4: SV6.7, SV10.7
MUL_SCL_5: SV7.7, SV11.7
MUL_SCL_6: SV8.7, SV12.7
MUL_SDA_1: SV1.8, SV3.8
MUL_SDA_2: SV2.8, SV4.8
MUL_SDA_3: SV5.8, SV9.8
MUL_SDA_4: SV6.8, SV10.8
MUL_SDA_5: SV7.8, SV11.8
MUL_SDA_6: SV8.8, SV12.8
unnamed: IC1.18 (O1), R1.1
unnamed: LED1.C, R1.2
unnamed: IC1.17 (O2), R2.1
unnamed: IC1.16 (O3), R3.1
unnamed: IC1.15 (O4), R4.1
unnamed: IC1.14 (O5), R5.1
unnamed: IC1.13 (O6), R6.1
unnamed: IC1.12 (O7), R7.1
unnamed: IC1.11 (O8), R8.1
unnamed: LED2.C, R2.2
unnamed: LED3.C, R3.2
unnamed: LED4.C, R4.2
unnamed: LED5.C, R5.2
unnamed: LED6.C, R6.2
unnamed: LED7.C, R7.2
unnamed: LED8.C, R8.2
unnamed: IC2.18 (O1), R9.1
unnamed: LED9.C, R9.2
unnamed: IC2.17 (O2), R10.1
unnamed: IC2.16 (O3), R11.1
unnamed: IC2.15 (O4), R12.1
unnamed: IC2.14 (O5), R13.1
unnamed: IC2.13 (O6), R14.1
unnamed: IC2.12 (O7), R15.1
unnamed: IC2.11 (O8), R16.1
unnamed: LED10.C, R10.2
unnamed: LED11.C, R11.2
unnamed: LED12.C, R12.2
unnamed: LED13.C, R13.2
unnamed: LED14.C, R14.2
unnamed: LED15.C, R15.2
unnamed: LED16.C, R16.2
unnamed: IC3.18 (O1), R17.1
unnamed: LED17.C, R17.2
unnamed: IC3.17 (O2), R18.1
unnamed: IC3.16 (O3), R19.1
unnamed: IC3.15 (O4), R20.1
unnamed: IC3.14 (O5), R21.1
unnamed: IC3.13 (O6), R22.1
unnamed: IC3.12 (O7), R23.1
unnamed: IC3.11 (O8), R24.1
unnamed: LED18.C, R18.2
unnamed: LED19.C, R19.2
unnamed: LED20.C, R20.2
unnamed: LED21.C, R21.2
unnamed: LED22.C, R22.2
unnamed: LED23.C, R23.2
unnamed: LED24.C, R24.2
SPWM_1_1: IC1.3 (I3), SV1.3, SV3.3
SPWM_1_2: IC1.4 (I4), SV1.4, SV3.4
SPWM_2_1: IC2.3 (I3), SV2.3, SV4.3
SPWM_2_2: IC2.4 (I4), SV2.4, SV4.4
SPWM_3_1: IC3.1 (I1), SV5.1, SV9.1
SPWM_3_2: IC3.2 (I2), SV5.2, SV9.2
SPWM_3_3: IC3.3 (I3), SV5.3, SV9.3
SPWM_3_4: IC3.4 (I4), SV5.4, SV9.4
SPWM_4_1: IC1.7 (I7), SV6.3, SV10.3
SPWM_4_2: IC1.8 (I8), SV6.4, SV10.4
SPWM_5_1: IC2.7 (I7), SV7.3, SV11.3
SPWM_5_2: IC2.8 (I8), SV7.4, SV11.4
SPWM_6_1: IC3.5 (I5), SV8.1, SV12.1
SPWM_6_2: IC3.6 (I6), SV8.2, SV12.2
SPWM_6_3: IC3.7 (I7), SV8.3, SV12.3
SPWM_6_4: IC3.8 (I8), SV8.4, SV12.4

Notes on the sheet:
Teensy Board
Matthew Chan 2014-10-16



Board: 2 copper layers, 75.7 x 64.3 mm, 65 parts (30 on the bottom side), 99 nets.

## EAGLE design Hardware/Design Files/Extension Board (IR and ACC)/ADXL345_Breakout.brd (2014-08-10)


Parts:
C1: 0.1uF; 0603-CAP
C2: 10uF; EIA3216
CIO: 0.1uF; 0603-CAP
JP1: M08; 1X08
JP2, JP3: STAND-OFF
JP4, JP5: FIDUCIAL1X2; FIDUCIAL-1X2
U2: ADXL345PATRICK; LGA14_1:1_PATRICK
U$2: LOGO-SFENEW; SFE-NEW-WEBLOGO
U$3: OSHW-LOGOS; OSHW-LOGO-S

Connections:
CS: JP1.3, U2.7 (CS)
GND: C1.2, C2.C (-), CIO.2, JP1.1, U2.2 (GND), U2.4 (GND), U2.5 (GND)
INT1: JP1.4, U2.8 (INT1)
INT2: JP1.5, U2.9 (INT2)
SCL: JP1.8, U2.14 (SCL)
SDA: JP1.7, U2.13 (SDA)
SDO: JP1.6, U2.12 (SDO)
VCC: C1.1, C2.A (+), CIO.1, JP1.2, U2.1 (VDD), U2.6 (VSS)

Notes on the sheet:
Updates:
* Non-cantilevered - added standoffs for stability
* Add decoupling cap - AD suggests 10uF and 0.1uF after upto 100Ohm resistance
Jim Lindblom
Revised by: Patrick Alberts
v14


Board: 2 copper layers, 20.3 x 15.2 mm, 11 parts (1 on the bottom side), 8 nets.

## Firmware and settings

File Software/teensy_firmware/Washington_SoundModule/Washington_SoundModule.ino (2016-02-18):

#define __USE_I2C_T3__
#define __USE_SERIALCOMMAND__
//#define __DEBUG__
#define DEBUG_FREQUENCY 500

#include <Audio.h>
#ifdef __USE_I2C_T3__
#include <i2c_t3.h> // Had to edit control_wm8731.cpp and control_sgtl5000.cpp to use i2c_t3.h instead of Wire.h
#else
#include <Wire.h>
#endif
#include <SPI.h>
#include <SD.h>

#include "T3Mac.h"

#include "sound_module.h"
#include "proximity.h"

#define N_SOUNDS 170

#ifdef __USE_SERIALCOMMAND__
#include <SerialCommand.h>
SerialCommand sCmd (&Serial);     // The demo SerialCommand object
#endif

// IR Sensor defines and variables
#define N_IR 2
#define IR_DECAY 0.001
#define PROXIMITY_THRESHOLD 0.9
Proximity ir[N_IR];
const uint8_t ir_pins[] = {A6, A14};

#ifdef __DEBUG__
// Debug messages
elapsedMillis sensorMessageDelay[2], sensorTrigMessageDelay[2];
#endif

const uint8_t NUM_BUFF = 6;

const uint8_t i2c_device_addr = 13;

uint8_t recvMsg[NUM_BUFF]; // first BUFF is always the message type




bool cycling = false;
uint32_t phase_time = millis();
uint32_t step_time = millis();
uint32_t next_step_time = 1;
uint8_t led_level[2] = {0, 0};
const uint8_t light_max_level = 255;

bool audio_cycling = false;
uint32_t audio_phase_time = millis();
uint32_t audio_step_time = millis();
uint32_t audio_next_step_time = 1;

void clearRecvMsg() {
	for (uint8_t i = 0; i < NUM_BUFF; i++) {
		recvMsg[i] = 0;
	}
}

enum OperationMode{
	SelfRunning,
	Manual,
	CBLA,
	Inactive = 255
};
//TODO: Watchdog Timer

// Heartbeat Timer
elapsedMillis heartbeatTimer;
bool heartbeatToggle;
SoundModule sound_module;

void setup() {

	Serial.begin(9600);

	// set up the indicator LED
	pinMode(LED_BUILTIN, OUTPUT);

	// clear buffer
	clearRecvMsg();

	// initialize the I2C
	//--- Set up the audio board ----
	sound_module.audio_board_setup();
	delay(100);

	Wire.begin(i2c_device_addr);
	delay(100);
	Wire.onReceive(receiveEvent);
	Wire.onRequest(requestEvent);

	delay(100);

	// sound_module.setVolume(10, 0, 0);

	for (int i = 0; i < N_IR; i++) {
		ir[i].init(ir_pins[i], IR_DECAY);
	}

	// Reads in the MAC address from T3Mac.h. Stored as uint8_t mac[6]
	read_mac();



#ifdef __USE_SERIALCOMMAND__
	sCmd.addCommand("VER", cmdVersion);          // Prints version
	sCmd.addCommand("BLINK", cmdBlink);          // Blinks lights
	sCmd.addCommand("VOL", cmdVolume);          // Changes volume
	sCmd.addCommand("MAC", cmdMAC);          // Prints MAC Address
	sCmd.addCommand("I2CSTAT", cmdI2CStatus);          // Prints I2C Status
	sCmd.addCommand("CONF", cmdConfigPrint);          // Prints Configuration
#endif
	
	
	enableWatchdog();
}

void receiveEvent(unsigned int bytes) {
	//Serial.print("Got a message from the Control Node: ");
	for (uint8_t i = 0; i < bytes; i++) {
		if (i >= NUM_BUFF) {
			//BUFFER Full
			break;
		}
		recvMsg[i] = Wire.read();
	}
	Serial.print("Received a message from the Control Node: ");
	for( int i=NUM_BUFF; i >= 0; i-- ){
		Serial.print(recvMsg[i]);
		Serial.print(" ");
	}
	switch (recvMsg[0]) {
	case SoundModule::CMD_CHECK_ALIVE:{
			Serial.print("| Check Alive");
			break;
		}
		// Analog read
	case SoundModule::CMD_READ_ANALOG:{ //TODO This should not need a message? DK
			Serial.print("| Read Analog Values");
			break;
		}
		// PWM Output
	case SoundModule::CMD_PWM_OUTPUT:{
			Serial.print("| PWM Output");
			break;
		}
		// Play Wav File
	case SoundModule::CMD_PLAY_WAV:{
			Serial.print("| Play Sound");
			break;
		}
	default:{
			break;
		}
	}
	Serial.println();
}

void requestEvent() {

	Serial.print("Got a request for data from the Control Node: ");
	Serial.println(sound_module.requested_data_type);

	switch(sound_module.requested_data_type){
	case SoundModule::CMD_CHECK_ALIVE: {
			Wire.write(lowByte(mac[0]));
			break;
		}
	case SoundModule::CMD_READ_ANALOG:
		for (uint8_t i = 0; i < 3; i++) {
			Wire.write(lowByte(sound_module.analog_data[i]));
			Wire.write(highByte(sound_module.analog_data[i]));
		}
		break;
		// else if (sound_module.requested_data_type == SoundModule::CMD_IS_PLAYING){
		// for (uint8_t i=0; i<4; i++){
		// Wire.write(sound_module.is_playing_L[i]);
		// }
		// for (uint8_t i=0; i<4; i++){
		// Wire.write(sound_module.is_playing_R[i]);
		// }
		// }
	}
}

uint32_t last_bg_on = millis();

// From other code in Washinton_Teensy
uint16_t loop_since_last_msg = 0;
const uint16_t keep_alive_thres = 10;
volatile uint16_t prev_operation_mode = 0;

uint16_t LOOP_PERIOD = 200;
elapsedMillis loop_time;

/*
Something in the loop crashes when running too quickly. 
Need further probing.
*/
void loop() {
	
	kickWatchdog(); // Make sure the Watchdog Timer doesn't expire

	uint32_t curr_time = millis();

	if (sound_module.receive_msg()){

		// parse the message and save to parameters
		sound_module.parse_msg();

		loop_since_last_msg = 0;

	}
	loop_since_last_msg++;

	
	// Change what you're doing based on the current operation mode
	if (sound_module.operation_mode != prev_operation_mode){
		Serial.print("Operation Mode: ");
		Serial.println(sound_module.operation_mode);
		prev_operation_mode = sound_module.operation_mode;
	}
	switch (sound_module.operation_mode){
	case SelfRunning: 
		//cbla_mode();
		self_running_test();
		break;
	case Manual:
		if (loop_since_last_msg > keep_alive_thres){
			inactive_mode();
		}
		else{
			manual_mode();
		}
		break;
	case CBLA:
		if (loop_since_last_msg > keep_alive_thres){
			//inactive_mode();
			self_running_test();
		}
		else{
			cbla_mode();
		}
		break;
	default:
		inactive_mode();
		break;
	}

	heartbeat();
	sound_module.cpu_analysis();


	#ifdef __USE_SERIALCOMMAND__
	sCmd.readSerial();     // We don't do much, just process serial commands
	#endif
	
	//This is important. Even with the sine wave instead of the microphone input, it failed without this delay.
	//wait if not enough time has passed
	int16_t remain_time = LOOP_PERIOD - loop_time;
	if (remain_time > 0){
		// Serial.print("Remaining Time: ");
		// Serial.println(remain_time);
		delay(remain_time);
	}
	loop_time = 0;
}

// Blink the indicator LED to know it's alive
void heartbeat() {
	if ( heartbeatTimer > 500 ) {
		heartbeatTimer = 0;
		heartbeatToggle = !heartbeatToggle;
		digitalWrite(LED_BUILTIN, heartbeatToggle);
	}
}

void self_running_test(){
	uint32_t curr_time = millis();
	//==== Basic Code ===
	
	//sound_module.getAudioState(0);

	//Update IR readings
	for (int i = 0; i < N_IR; i++) {
		ir[i].read();
	}

	bool bg_on = false;

	if (curr_time - last_bg_on > 1000){
		bg_on = random(1, 10) <= 2;

		last_bg_on = millis();

	}

	// Test proximity sensors and play sound if seen
	for( int i=0; i < N_IR; i++){
		if ((ir[i].value() > PROXIMITY_THRESHOLD)) {
			#ifdef __DEBUG__
			if( sensorTrigMessageDelay[i] > DEBUG_FREQUENCY ){
				Serial.print("Proximity Sensor ");
				Serial.print(i);
				Serial.print(" Found: reading ");
				Serial.print(ir[i].reading);
				Serial.print(" | normal ");
				Serial.print(ir[i].value());
				Serial.print(" | ");
				Serial.print(ir[i].limits.decay_minimum());
				Serial.print(" | ");
				Serial.print(ir[i].limits.average());
				Serial.print(" | ");
				Serial.println(ir[i].limits.decay_maximum());
				sensorTrigMessageDelay[i] = 0;
			}
			#endif
			
			int sound_id = random(1, N_SOUNDS);
			//concatenate file id and extension to a string
			String filename_string = String(sound_id) + ".wav";
			char filename [filename_string.length()]; // allocate memeory the char_arr
			filename_string.toCharArray(filename, filename_string.length() + 1); // convert String to char_arr

			sound_module.playWav(filename, i+1, 0, 1);

		}
		#ifdef __DEBUG__
		if( sensorMessageDelay[i] > DEBUG_FREQUENCY ){
			Serial.print("Proximity Sensor ");
			Serial.print(i);
			Serial.print(": reading ");
			Serial.print(ir[i].reading);
			Serial.print(" | normal ");
			Serial.print(ir[i].value());
			Serial.print(" | ");
			Serial.print(ir[i].limits.decay_minimum());
			Serial.print(" | ");
			Serial.print(ir[i].limits.average());
			Serial.print(" | ");
			Serial.println(ir[i].limits.decay_maximum());
			sensorMessageDelay[i] = 0;
		}
		#endif
	}

	//>>>> Light <<<<<
	//starting a cycle
	if (( ir[0].value() > PROXIMITY_THRESHOLD || ir[1].value() > PROXIMITY_THRESHOLD || bg_on) && !cycling) {
		Serial.println("starting cycle");
		cycling = true;
		phase_time = millis();
		step_time = millis();
		next_step_time = 2;
	}
	else if (cycling) {

		volatile uint32_t cycle_time = curr_time - phase_time;

		//ramping down
		// if reaches the full period, restart cycle
		if (cycle_time > 3000) {

			volatile uint32_t ramping_time = curr_time - step_time;

			if (ramping_time > next_step_time) {
				for (uint8_t output_id = 0; output_id < 2; output_id++) {
					if (led_level[output_id] > 0)
					led_level[output_id] -= 1;
				}
				next_step_time += 1;
				step_time = millis();
			}

			bool end_cycling = true;
			for (uint8_t output_id = 0; output_id < 2; output_id++) {
				end_cycling &= led_level[output_id] <= 0 ;
			}
			if (end_cycling) {
				cycling = 0;
			}

		}
		//hold steady
		else if (cycle_time > 2000) {

		}
		// ramping up
		else {
			volatile uint32_t ramping_time = curr_time - step_time;

			if (ramping_time > next_step_time) {

				if (led_level[0] < light_max_level)
				led_level[0] += 1;
				if (cycle_time > 500) {
					if (led_level[1] < light_max_level)
					led_level[1] += 2;
				}
				next_step_time += 1;
				step_time = millis();
			}

		}
	}

	sound_module.set_output_level(0, led_level[0]);
	sound_module.set_output_level(1, led_level[1]);
}

void manual_mode(){}
void inactive_mode(){}
void cbla_mode(){
	
	sound_module.cbla_behaviour();
	
}

#ifdef __USE_SERIALCOMMAND__
void cmdVersion() {
	Serial.println("TEENSY SOFTWARE COMPILED: " __DATE__ " " __TIME__);
}

void cmdBlink() {
	Serial.println("Blinking...");
	for ( int i = 0; i < 10; i++ ) {
		sound_module.set_output_level(0, 255);
		sound_module.set_output_level(1, 0);
		delay(10);
		sound_module.set_output_level(0, 0);
		sound_module.set_output_level(1, 255);
		delay(10);
	}
	sound_module.set_output_level(0, 0);
	sound_module.set_output_level(1, 0);
	Serial.println("Done Blinking...");
}

// Changes volume to x in "VOL x" where x=0-9
void cmdVolume(){
	int vol = 0;
	char *arg;

	arg = sCmd.next();
	if( arg != NULL ){    
		vol = atoi(arg);
		sound_module.sgtl5000_1.dacVolume(((float)vol)/9.0); // Digitally adjusts volume from 0.0-1.0
		
		Serial.print("Set volume to ");
		Serial.println(((float)vol)/9.0);
	} else {
		Serial.println("Volume could not be set. Argument was NULL. [" __FILE__ ": " "__LINE__" "]");
	}

}

// Prints the Teensy's MAC address
void cmdMAC(){
	print_mac();
	Serial.println();
}

// Print the Code's Configuration Flags
void cmdConfigPrint(){
	Serial.print("Config: ");
	Serial.print("Debug[");
#ifdef __DEBUG__
	Serial.print("y");
#else
	Serial.print("n");
#endif
	Serial.print("] i2c_t3[");
#ifdef __USE_I2C_T3__
	Serial.print("y");
#else
	Serial.print("n");
#endif
	Serial.print("] SerialCommand[");
#ifdef __USE_SERIALCOMMAND__
	Serial.print("y");
#else
	Serial.print("n");
#endif
	Serial.println("]");

}

// Print the I2C Status
void cmdI2CStatus(){
	print_i2c_status();
}

//
// print I2C status
//
void print_i2c_status(void)
{
	switch(Wire.status())
	{
	case I2C_WAITING:  Serial.print("I2C waiting, no errors\n"); break;
	case I2C_ADDR_NAK: Serial.print("Slave addr not acknowledged\n"); break;
	case I2C_DATA_NAK: Serial.print("Slave data not acknowledged\n"); break;
	case I2C_ARB_LOST: Serial.print("Bus Error: Arbitration Lost\n"); break;
	case I2C_TIMEOUT:  Serial.print("I2C timeout\n"); break;
	case I2C_BUF_OVF:  Serial.print("I2C buffer overflow\n"); break;
	case I2C_SENDING:  Serial.print("I2C sending\n"); break;
	case I2C_SEND_ADDR: Serial.print("I2C send addr\n"); break;
	case I2C_RECEIVING: Serial.print("I2C receiving\n"); break;
	case I2C_SLAVE_TX: Serial.print("I2C slave TX\n"); break;
	case I2C_SLAVE_RX: Serial.print("I2C slave RX\n"); break;
	default:           Serial.print("I2C busy\n"); break;
	}
}
#endif

void enableWatchdog(){
	WDOG_UNLOCK = WDOG_UNLOCK_SEQ1;
	WDOG_UNLOCK = WDOG_UNLOCK_SEQ2;
	delayMicroseconds(1); // Need to wait a bit..
	WDOG_STCTRLH = 0x0001; // Enable WDG
	WDOG_TOVALL = 2000; // The next 2 lines sets the time-out value. This is the value that the watchdog timer compare itself to in milliseconds
	WDOG_TOVALH = 0;
	WDOG_PRESC = 0; // This sets prescale clock so that the watchdog timer ticks at 1kHZ instead of the default 1kHZ/4 = 200 HZ
}

void kickWatchdog(){
	noInterrupts();
	WDOG_REFRESH = 0xA602;
	WDOG_REFRESH = 0xB480;
	interrupts();
}

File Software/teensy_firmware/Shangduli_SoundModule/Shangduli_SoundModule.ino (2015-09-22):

// *** Listening for a specific sound while running Vinegar Battery to sound module SOUND MODULE ***
// Vinegar battery controls delay between triggering of sounds
// Code to perform basic control of the sound module including:
// - 3 analog inputs
//    - A1p = IR
//    - A2p = IR
//    - A3p = Vinegar Battery
// - 2 digital trigger inputs
// - 2 audio channel outputs
// - 2 audio channel inputs
// - 2 low power PWM reflex channels

//*** Variable Initialization ***
// Load required libraries for Teensy Audio Board, I2C communication, and SD Card Reading
#include <Audio.h>
#include <Wire.h>
#include <SPI.h>
#include <SD.h>
#include <String.h>

// Establish Input and Output Pin variables for Teensy
// Analog Inputs
const int A1p = A6;
const int A2p = A7;
const int A3p = A14;

// PWM ouput pins for reflex channels
const int R1 = 3;
const int R2 = 4;

// Digital Trigger Input Pins
const int DT1 = 1;
const int DT2 = 2;

// Signal output pin 
const int SOUT1 = 5;

// Establsh Variables used in signal processing
const int bins = 512; // Number of bins in FFT
float fs = 44117.647; //Sampling rate
float dF = fs/bins/2.0; // width of FFT bin in Hz
float sf = 3.0; // Scaling Factor of FFT values in DB calculation
float lowF = 200; // Low frequency cutoff for stats calculations
float highF = 6000; // High Frequency cutoff for FFT

float SCG; // Spectral Center of Gravity
float aV;
int mFdata[2];
float cf[bins];
float valFFT[bins];
float dBvalFFT[bins];

boolean printSerial = true;

elapsedMillis T1; // timer object
elapsedMillis T2; // timer object

// Vinegar Battery Variables
int VBdelay = 10000; // Length of time in ms for VB to delay
uint32_t VBmax = 50000; // Maximum delay length in ms 

boolean UNBLOCKAUDIO = HIGH; // BLOCK AUDIO PLAYBACK
int blockT = 2000; // Time to block audio for in milliseconds

//Define 8 Independent Wavfiles for playback in two 4-channel mixers
AudioPlaySdWav           playWav1;       // mixer1 - Left Channel
AudioPlaySdWav           playWav2;       
AudioPlaySdWav           playWav3;       
AudioPlaySdWav           playWav4;       

AudioPlaySdWav           playWav5;       // mixer2 - Right Channel
AudioPlaySdWav           playWav6;       
AudioPlaySdWav           playWav7;       
AudioPlaySdWav           playWav8;       

AudioInputI2S            i2s1;           // set up audio input variable from LINE-IN
AudioAnalyzeFFT1024      fft1024_1;      // FFT input - Left Channel
  //AudioAnalyzeFFT1024      fft1024_2;      // // FFT input - Right Channel - LIBRARY CURRENTLY DOESN'T support this (so leave it commented out)

AudioMixer4              mixer1;         // mixer1 - Left Channel
AudioMixer4              mixer2;         // mixer1 - Right Channel
AudioOutputI2S           i2s2;           // set up audio output through LINE-OUT

AudioConnection          patchCord2(playWav1, 0, mixer1, 0); //Set wav file inputs to mixer1
AudioConnection          patchCord7(playWav2, 0, mixer1, 1);
AudioConnection          patchCord5(playWav3, 0, mixer1, 2);
AudioConnection          patchCord4(playWav4, 0, mixer1, 3);

AudioConnection          patchCord8(playWav5, 0, mixer2, 0); //Set wav file inputs to mixer2
AudioConnection          patchCord6(playWav6, 0, mixer2, 1);
AudioConnection          patchCord3(playWav7, 0, mixer2, 2);
AudioConnection          patchCord1(playWav8, 0, mixer2, 3);

AudioConnection          patchCord9(i2s1, 0, fft1024_1, 0); // FFT of LINE-IN Left Channel
//AudioConnection          patchCord10(i2s1, 1, fft1024_2, 0); // FFT of LINE-IN Left Channel - leave commented

AudioConnection          patchCord11(mixer1, 0, i2s2, 0); // Output mixer1 to LINE-OUT left channel
AudioConnection          patchCord12(mixer2, 0, i2s2, 1); // Output mixer2 to LINE-OUT right channel

AudioControlSGTL5000 sgtl5000_1; //Initialize LINE-OUT control element


//*** SETUP LOOP ***
void setup() {
  Serial.begin(9600);

  // Audio connections require memory to work.  For more
  // detailed information, see the MemoryAndCpuUsage example

  AudioMemory(20); // Establish Audio Memory

  sgtl5000_1.enable(); // Enable LINE-OUT
  sgtl5000_1.volume(1.0); //Set Iniitial LINE-OUT Gain
  fft1024_1.windowFunction(AudioWindowHanning1024); // Define the window applied to FFT
	
  // set up the trigger pins
  pinMode(DT1, INPUT_PULLUP);
  pinMode(DT2, INPUT_PULLUP);
  
  // set up the signal output pins
  pinMode(SOUT1, OUTPUT);
  digitalWrite(SOUT1, LOW);

  SPI.setMOSI(7); //Sets pin for TAB - Don't change
  SPI.setSCK(14); //Sets pin for TAB - Don't change

  // Check SD card is present and readable
  if (!(SD.begin(10))) {
    // stop here, but print a message repetitively
    while (1) {
      Serial.println("Unable to access the SD card");
      delay(500);
    }
  }
  WDOG_UNLOCK = WDOG_UNLOCK_SEQ1;
  WDOG_UNLOCK = WDOG_UNLOCK_SEQ2;
  delayMicroseconds(1); // Need to wait a bit..
  WDOG_STCTRLH = 0x0001; // Enable WDG
  WDOG_TOVALL = 2000; // The next 2 lines sets the time-out value. This is the value that the watchdog timer compare itself to.
  WDOG_TOVALH = 0;
  WDOG_PRESC = 0; // This sets prescale clock so that the watchdog timer ticks at 1kHZ instead of the default 1kHZ/4 = 200 HZ

}
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

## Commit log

2014-08-08 Initial Commit
    This commit included the library for which the devices, symbols, and
    footprint relevant to this project resides. Also added the initial
    schematic diagram for the Tentacle module.
    [tentacle_module.brd, tentacle_module.sch]
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2014-08-08 fixed the indicator LED error.
    The negative pin of the LED was connected to the ground and the positive
    pin was connected to the drain. That wouldn't have worked.
    Also rotated the longer labels to make them fit nicer.
    [tentacle_module.brd, tentacle_module.sch]
2014-08-08 Tentacle board improvement
    Added Schottky diodes for reverse voltage protection
    Added headers fro the RJ45 jack for more flexibility in terms of
    connectors
    Added modified the appearance of the schematic and added some more
    comments.
    [tentacle_module.brd, tentacle_module.sch]
2014-08-09 Positioned components on Tentacle PCB
    Fixed some mistakes on the schematics
    Remove one pair of the headers for the RJ45 port
    Placed components on the PCB.
    [tentacle_module.brd, tentacle_module.sch]
2014-08-09 Added mounting holes to Tentacle PCB
    [tentacle_module.brd]
2014-08-09 Changed capacitor footprint from 1210 to 1206
    [tentacle_module.brd, tentacle_module.sch]
2014-08-09 Added the RJ45 connector
    [RJ45_connector_y.brd, RJ45_connector_y.sch, tentacle_module.brd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]
2014-08-10 Routed the RJ45 connector with side and top headers
    Also added the accelerometer chip to the library
    [ADXL345_Breakout.brd, ADXL345_Breakout.sch, RJ45_connector.brd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]
2014-08-10 Changed location of the header to make it much easier to router
    [RJ45_connector.brd, RJ45_connector.sch, tentacle_module.brd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]
2014-08-10 Moved the location of the header
    [tentacle_module.brd]
2014-08-10 started on the Tentacle tip board
    [tentacle_tip.brd, tentacle_tip.sch]
2014-08-11 Completed routing the tentacle tip board
    [tentacle_tip.brd]
2014-08-11 Minor update of the Tentacle Tip board
    [tentacle_tip.brd]
2014-08-11 Added labels to pins on the silkscreen
    [tentacle_tip.brd]
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2014-08-11 Updated the Tentacle module schematic
    [tentacle_module.brd, tentacle_module.sch]
2014-08-12 Preliminary part placement for the tentacle board
    [tentacle_module.brd, tentacle_module.sch]
2014-08-12 Finished routing the Tentacle module board
    Not changing it!
    [tentacle_module.brd, tentacle_module.sch]
2014-08-12 Fixed up the Tentacle tip board
    routed the airwires that I forgot
    [tentacle_tip.brd]
2014-08-12 Modified labels and silkscreen
    [tentacle_tip.brd, tentacle_tip.sch]
2014-08-12 made modifications to board design and correct errors
    [DRILEGEND.CFG, Protocell_module.sch, tentacle_module.brd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]
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2014-08-12 Added Exar and TI libraries
    [Protocell_module.brd, Protocell_module.sch]
2014-08-12 Merge remote-tracking branch 'origin/master'
    Conflicts:
    PCB Design/CBLA_Test_bed_Library.lbr
    [Teensy_Board.sch]
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2014-08-12 Restore Teensy Board schematic
    [Teensy_board.sch]
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2014-08-12 Fixed CBLA Lib
    [Teensy_Board.brd, Teensy_board.sch]
2014-08-12 Finished updating the Tentacle board
    not polished yet though
    [tentacle_module.brd, tentacle_module.sch]
2014-08-13 removed the unnecesssary by-pass cap by the v-reg
    [tentacle_module.brd, tentacle_module.sch]
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2014-08-13 Modified Tentacle tip board to make pins longer
    [tentacle_tip.brd, tentacle_tip.sch]
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2014-08-13 Finished schematic and part placements
    [Protocell_module.brd, Protocell_module.sch]
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2014-08-13 fixed the error with order of headers for IR sensor
    [tentacle_tip.brd, tentacle_tip.sch]
2014-08-13 Added the BOM and part number for the Tentacle module
    [BOM.xlsx, tentacle_module_BOM.csv]
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2014-08-13 Polished silkscreen on protocell board
    also add prefix to a part in library
    [Protocell_module.brd, Protocell_module.sch]
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2014-08-13 Swapped the SDA and SCL pins on the Tentacle tip connector
    [tentacle_module.brd, tentacle_module.sch, tentacle_tip.brd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]
2014-08-13 Changed the 10uF capacitor for the ADXL345 to 1206 package
    [BOM.xlsx]
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2014-08-20 removed the RJ45 connector; moved Tentacle tip to its own folder
    [ADXL345_Breakout.brd, ADXL345_Breakout.sch, RJ45_connector.brd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]
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2014-08-26 Fixed a TeensyInterface bug
    it will now wait until the previous cmd_obj process before writing the
    next one for each Teensy
2014-08-28 Modified Teensy Tip silkscreen error
    [tentacle_tip.brd]
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2014-09-12 fixed the i2c hanging problem
    instantiate i2c_t3 at the object rather than in the library
    [SMA_BOARD.ino, behaviours.cpp, teensy_unit.cpp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]
2014-09-12 got it sending accelerometer measurements
    also not freeze after unplugging it. but won't restart
    [behaviours.cpp, behaviours.h, teensy_unit.cpp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]
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2014-09-12 fixed bug: Tentacle's analog wasn't sent to PC correctly
    Note: Accelerometer only hangs when the PC keeps trying to talk to it!
    [behaviours.cpp, teensy_unit.cpp]
2014-09-17 testing code with no accelerometer fails
    [behaviours.cpp, behaviours.h, teensy_unit.cpp]
2014-09-23 Edited the wave_table class
    Removed amplitude
    Fixed bugs where outputs get round off
    Fixed bug that omitted transition between last and first bit
    Removed extra declarations that were causing problems
    [wave_table.cpp]
2014-09-25 Code and video for stress test
    The system consists of two bright led, three vibration motors, and six
    SMA wires. I have those actuator running in loop while polling all the
    sensors
    [behaviours.cpp, behaviours.h]
2014-10-03 Added the prototype version to archive
    Note some small modifications been made after production that are saved
    in this archieve
    [ADXL345_Breakout.brd, ADXL345_Breakout.sch, Protocell_module.brd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]
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2014-10-03 Added 4 more power ports; added pull up resistor; made a power plate for the power
    [Teensy_Board.brd, Teensy_board.sch]
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2014-10-06 Added resistor value to the i2c pull up
    [Teensy_board.sch]
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2014-10-06 Fixed the power plate error and misplacement of port #4
    [Teensy_Board.brd]
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2014-10-17 Made Teensy Board smaller by moving the RJ45 connector to another board
    [Teensy_Board.brd, Teensy_Board_Connectors.brd, Teensy_Board_Connectors.sch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]
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2014-10-27 Updated BOM and made BOM for Bittele PCB
    [BOM.xlsx, BOM_Bittele.xls]
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2014-10-28 It now works without plugging into USB
    Turned out that when it is not plug, it always "received msg". So it
    stuck in the really long loop in the init() code. I now made the quit
    counter to 100, so it starts quicker.
    [HK_Unit_Teensy.ino, teensy_unit.cpp]
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2014-12-08 fix the commenting error
    [behaviours.h]
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2014-12-08 changed archived files into zip
    this to avoid them being double counted in the language stats
    [CBLA_Testbed_Unit_Teensy.ino, SMA_BOARD.ino, behaviours.cpp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]
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2014-12-09 Fixed that read and compose msg bugs
    - send from send_data_buff instead of recv_data_buff
    - use temp_val to compose 16-bit integers from two 8-bit intergers
    [behaviours.cpp, behaviours.h]
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2014-12-17 Added ULN2803 with SOP18 PKG for the connector board
    [Teensy_Board_Connectors.brd, Teensy_Board_Connectors.sch]
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2014-12-18 Updated Teensy Board and Connector Board design
    - fixed broken connection
    - makes everything 45 degrees bend
    - moved the RJ45 connectors a bit to the right so they don't interfere
    with the power header
    - connect common pin to _5V
    - added power and ground pour
    [Teensy_Board.brd, Teensy_Board_Connectors.brd, Teensy_Board_Connectors.sch]
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2014-12-22 Moved Sound Detector Board Pins
    Spread out pins on sound detector boards so that the boards don’t
    physically interfere with each other when 2 are mounted at the same
    time.
    [Sound.brd]
2015-01-06 interface with hardware added multiple CBLA engines. one for each node A node may only use a subset of all avaliable actuators
    [Teensy_Board.brd, Teensy_Board.csv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]
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2015-01-08 Changed names
    from Teensy Board to Control Module
    from Protocell Module to Lumination Module
    [Control_Module.brd, Control_Module.sch, Lumination_Module.brd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]
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2015-01-08 Renamed from Teensy Board Connector to RJ45 Connectors Board
    [RJ45_Connectors_Board.brd, RJ45_Connectors_Board.sch]
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2015-01-09 Added protocell to test behaviour
    fixed the bug where the ir_range is only an 8-bit number. It now
    supports longer range
    [behaviours.cpp]
2015-01-09 Compiled files needed for PCB fabrication, and assembly,
    Also the BOM and the parts number that we are shipping.
    [BOM_Bittele.xls, Control_Module.brd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]
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2015-01-15 removed changePriority
    not changing the threads to "real-time-mode"
    this remove some cross-platform issues
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2015-01-21 integrated the loop_delay into the report() function
    also added a read_interval to avoid looping too fast
    added derived parameters
    allowed configuration of split_thres, mean_err_thres, and saving_freq
    when instantiating the CBLA thread
    made each tentacle to accelerometer pair to run on its own CBLA loop.
    but all three loops are sychronized.
    Added new request type, "read-only" that doesn't update the Teensy with
    new parameters
    [behaviours.cpp, behaviours.h]
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2015-01-30 Added "write-only" parameter
    it is a flag to let the Teensy know that it doesn't need to sample the
    sensor before replying
    used the 63rd byte, so now content can only be 60 byte long.
    [behaviours.cpp, behaviours.h, teensy_unit.cpp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]
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2015-02-01 Optimized communication - reduced number of messages sent Debugged the multi-threaded communication process Sync_barrier is now doing the timing control and the actual communcation with interactive_c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
2015-02-03 Moved Fabrication files one level up and renames PCB Design Folder to simply Design File
    [31003A1_BOM_ML_modified.xlsx, 31324A1_BOM_MB.xlsx, 31324A1_BOM_MB_15_01_16.xlsx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]
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2015-02-03 added operation modes to Teensy's firmware in each behaviour, send a message indicating the desired operation mode before starting CBLA bug fix: it wasn't allowing '0' as an output
2015-02-03 added an EOL Tool
    only tests the Tentacle and Protocell's actuators
    doesn't output to files yet
    [behaviours.cpp, behaviours.h]
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2015-02-07 discovered problem with using timer interrupt to check msgs
    it seems to interfere the operation of multiplexed PWM (it might use the
    same timer interrupts)
    revert back to using polling and have write-only flag (now that mean
    msg_setting != 0_
    [behaviours.cpp, behaviours.h, teensy_unit.cpp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]
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2015-02-10 Added lists that specify which Teensy to be included and which Teensy must be present in the CBLA system. Unused Teensy's will be killed and missing Teensy's will raise an error.
2015-02-11 added a DataCollector class that collect data in to DataCollection format This is a more flexible way of collecting file (only one file per run, instead of one per object) Have a thread that watch fo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
2015-02-17 Modified how values are calculated, added artificial noise
    For Oudeyer action selection method, change it to randomly select a M
    from a list of M's that are tied for the highest L
    Changed Expected Reward to Value and it is incremented with a learning
    rate
    Initialized with 0 mean error and 0 value; this way, each region starts
    with bad estimate; this encourage exploration at the beginning
    keeping track of actual rate of exploration
    Added artificially injected noise
2015-02-18 Limited the Protocell LED to 100
    When it was at max and with the flask on, it was burnt out probably due
    to overheating.
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2015-02-19 Fixed bugs
    Raise error when Mandatory Teensy are missing
2015-02-22 Test Bed initial experiment set up
    Tuned parameters to enable expected behaviours
    Added Idling preferred feature; it will do idle when the reward is low
    in all region
    The idling reward is smoothed by taking average over a window of time.
    Also, the it has to be non-idle for period time after breaking out of
    idle mode
    # of exemplars threshold will increase every split
    If split quality as measured by within-group variance is low, it won't
    split. The threshold inherited from parents times a decay factor which
    approaches one.
    Added a function that save figures to files
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2015-03-25 Fixed the bug in communication protocol that does not transmit message to active reflex actuators correctly
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2015-03-30 raise custom error message when Teensy device is in used
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2015-04-01 fixed bud - it's now displaying accelerometer values properly
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2015-04-01 change the i2c timeout to 1000us (as it didn't work when it was set to 100)
    [teensy_unit.h]
2015-04-01 fixed bug: it was combining messages from multiple teensy's together
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2015-04-15 added more lock to data_collect since it can be access by multiple threads not saving exemplars all the time as this takes too much memory (save time by not saving it at ll instead of deleting afterw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
2015-04-28 prevent error message when Teensy was found but was not responding at the beginning
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2015-05-08 fixed the freezing problem by having the hmi living and being called exclusively in the main thread the behaviour thread does create the terminate thread anymore. It will be called by the main thread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
2015-06-18 limited the LED Driver's output to [0, 255] fixed the variable names errors Displayed the generic CBLA node on gui Add the value of the input to the error messaage
2015-06-27 removed the custom "get_possible_action" added robot_config as parameters added led driver for reflex actuators as well fix the problem that LEDs all become one changed names of the teensy's
2015-06-27 fixed bug: the communication for Light type hardcoded "2".
    [behaviours.cpp]
2015-06-28 gui "destroy" instead of "quit" increase number of button per column fix the "after" bug for basic_gui as well.
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2015-07-13 added new hardware fabrication files Lumination module renamed Light Module
    [Light_Module.brd, Light_Module.sch]
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2015-07-22 added mass cleaning when queue reached certain threshold to prevent memory from over flowing
2015-07-22 added that prevent training when there aren't enough samples region splitter removed unused classes; made the splitting a bit more efficient; also the scoring method for selecting best_cut is changed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
2015-09-01 updated the BOM by highlighting the components we have in stock
    [BOM_ControlModule.xlsx, Light_Module_BOM.xlsx, RJ45_Connectors_Board_BOM.xlsx]
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2015-09-03 Integrated the switch_mode feature in the GUI Fixed a bug where S0 and M0 becomes initial value when restoring from previous sessions
2015-09-11 fixed typo in comment. now print 'Plotted proximal activation...' instead of 'total'
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2015-10-16 Fixed a bug that caused the firmware to crash. NUM_FIN, NUM_CRICKET, NUMLIGHT needs to be scoped properly.
    [Washington_Teensy.ino]
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2015-10-28 tested the cricket_node changed to manual mode fixed but that report both IR as IR0
    [washington_prescripted.py]
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2015-11-30 filter activity ratio through a gaussian so that when there are lots of activation, the probability of activating will decrease. this avoid a self enforcing cycle of increasing activity
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2015-12-17 added sound node to the prescritped code fixed one bug in the sound node's communicaiton protocol
    [washington_prescripted.py]
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2015-12-17 added test teensy and correct serial numbers
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2016-01-15 Added the Statistic Library into the node definition and code to use it into the self-directed behaviour. Added a test function into the SerialCommand list to turn on lights. DOES NOT WORK YET.
    [Washington_Teensy.ino]
2016-01-19 Removed unnecessary headers. Fixed SerialCommand.
    [Washington_SoundModule.ino, sound_module.cpp]
2016-01-19 Fixed missing curly brace on if statement.
    [sound_module.cpp]
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2016-01-19 Fixed a problem with the way the pin was being set. NONE OF THE PREVIOUS COMMITS WILL WORK BECAUSE OF THIS.
    [Washington_SoundModule.ino]
2016-01-19 Fixed the decaying property of the adaptive threshold, which was NOT SET
    [Washington_SoundModule.ino]
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2016-01-22 Revert "Some edits to restore the functionality to before merging in the major reorganizational changes"
    This reverts commit b5d5aa4749c2ca7dfbae983437dfe0db3360e06f.
    [Washington_Teensy.ino, sound.cpp]
2016-01-22 Changed the delay so that BLINK does not trigger a watchdog timer reset
    [Washington_SoundModule.ino]
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2016-01-26 consolidate all the core Python libraries into pyHylozoic3
    [cbla_isolated_2016-01-26_12-33-13.csv, cbla_isolated_2016-01-26_12-36-30.csv]
2016-01-26 added the CBLa Node for the Washington Sound Test Bed; bug fix for the cbla module
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2016-01-28 changed back to fft 1024 and it doesn't crashed when communicating anymore
    [sound_module.cpp, sound_module.h]
2016-01-28 added loop period which limit how fast the loop in the .ino file can run. Turned out if it's running to fast, it crashses.
    [Washington_SoundModule.ino, sound_module.cpp, sound_module.h]
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

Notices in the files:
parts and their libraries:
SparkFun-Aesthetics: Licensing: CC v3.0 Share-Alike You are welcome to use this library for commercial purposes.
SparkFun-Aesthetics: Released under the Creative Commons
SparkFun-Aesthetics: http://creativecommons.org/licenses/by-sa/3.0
